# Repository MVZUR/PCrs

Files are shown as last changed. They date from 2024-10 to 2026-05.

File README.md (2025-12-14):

# PCrs
Onboard Computer & System for cheap 4T scooters to improve safety and expand functionalities. <br>
It can be also used with 2T scooters but code modifications is necessary - particularly the RPM counting fragment.

Vehicle used for testing: Benda BD50QT-14

# Functionalities:
- date & time  
- automatic lights (daily / pass)
- hazard warning lights
- RPM indicator
- engine temperature indicator
- stand sensor controll
- tamper alarm
- accelleration measurement
- envirionment condition measurement & alerts

# Revisions:
- <b>v1.0</b> - *do not use* - the first version of the Computer. Many mistakes were made in this version, what makes it unable to use.
- <b>v1.1</b> - *do not use* - works on prototype board, but doesn't work in the target system. Computer got damaged but its unable to diagnose due to hermetic case.
- <b>v2.0</b> - *do not use* - the second version of the Computer. Only power section tested.
- <b>v2.1</b> - *do not use* - second version of the Computer with improved power section. Works in laboratory environment. LCD power controll not working properly.
- <b>v3.0</b> - *under tests* - the third version of the Computer.

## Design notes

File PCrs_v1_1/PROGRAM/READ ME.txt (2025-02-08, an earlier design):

Clock time can be set through physical buttons on dashboard by User in this version of the code (instead of using programmer and change it in code).

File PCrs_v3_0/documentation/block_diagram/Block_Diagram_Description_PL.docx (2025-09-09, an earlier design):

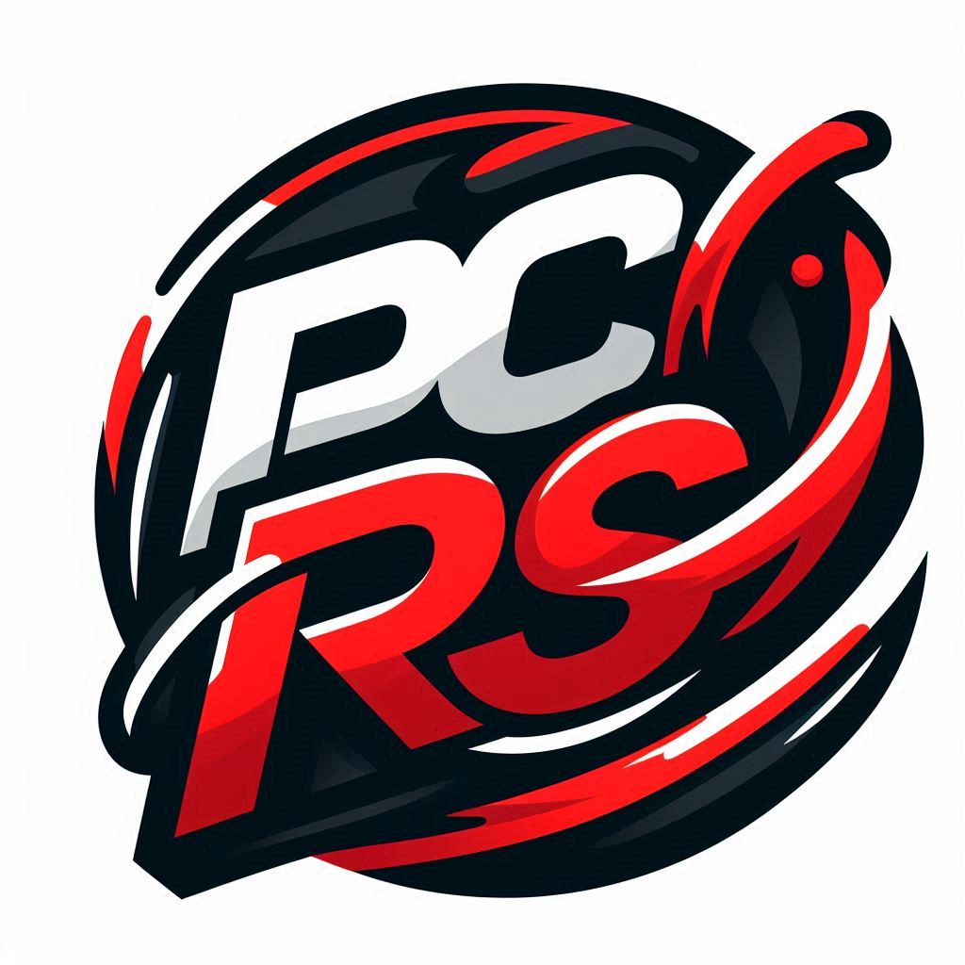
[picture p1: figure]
Obraz zawierający logo, Grafika, symbol, clipart Zawartość wygenerowana przez sztuczną inteligencję może być niepoprawna.

PCrs v3.0

Komputer pokładowy dla jednośladów

Opis połączeń na podstawie schematu blokowego

Opracował: Maksymilian Mazur

1. Alternator:
(źródło zasilania AC)

Źródło napięcia AC generowane przez stator silnika podczas jego obrotu. Jest wykorzystywane do rozruchu silnika, a także podawane na prostownik w celu jego wyprostowania.

Oznaczenie sygnału na schemacie blokowym: AC

2. Rectifier:
(prostownik)

Wyprostowane napięcie z alternatora o wartości +12V. Wartość prądu dostarczanego przez prostownik ściśle zależy od prędkości obrotowej silnika. Prostownik dostarcza zasilanie do świateł pojazdu (diody LED oraz żarówka światła drogowego/mijania).

Oznaczenie sygnału na schemacie blokowym: +12V rect

3. Scooter Battery:
(akumulator, źródło zasilania +12V)

Akumulator zapewnia lokalne napięcie +12V i prąd dostarczany w sposób ciągły. Napięcie to zostaje wykorzystane jako detekcja przekręcenia klucza w stacyjce, zasilanie klaksonu, modułu migacza, a także jest podawana na linię zabezpieczającą dalsze peryferia i wykorzystującą w tym celu układ E-Fuse.

Oznaczenie sygnału na schemacie blokowym: +12V bat

4. E-Fuse:
(zabezpieczona linia zasilania)

Zabezpieczone napięcie zasilania +12V, dostarczane do przetwornicy typu buck, obniżającej napięcie do +5V, a także do cewek wszystkich przekaźników w systemie, pracujących z napięciem +12V.

Zastosowane zabezpieczenia:

- przed zbyt dużym prądem (nadprądowe)
- przed zbyt dużym napięciem (nadnapięciowe)
- zabezpieczenie przed odwrotną polaryzacją (reverse-polarity)
- filtracja napięcia zasilania
- zastosowanie kondensatorów magazynujących energię

Oznaczenie sygnału na schemacie blokowym: +12V protected

5. Buck Converter 12V to 5V:
(przetwornica impulsowa, źródło zasilania +5V)

Przetwornica impulsowa pozwala na obniżenie zabezpieczonego napięcia +12V do napięcia +5V, przy niskim współczynniku strat. Odpowiada za zasilanie wszystkich peryferiów pracujących z napięciem +5V (aktualnie brak). Dostarcza także napięcie do regulatora liniowego LDO, obniżającego napięcie do +3.3V.

Oznaczenie sygnału na schemacie blokowym: +5V

6. LDO Regulator 5V to 3.3V:
(regulator liniowy, źródło zasilania +3.3V)

Regulator liniowy LDO zapewnia zasilanie +3.3V, obniżając napięcie +5V z przetwornicy typu buck. Napięcie +3.3V po uprzedniej filtracji jest dostarczane do głównego mikrokontrolera sterującego całym systemem, a także czujnika warunków środowiskowych, oraz akcelerometru.

Oznaczenie sygnału na schemacie blokowym: +3.3V

7. CR2032 RTC Battery 3V:

(bateria zasilająca moduł zegara czasu rzeczywistego)

Bateria typu CR2032 o napięciu 3V zamocowana w podstawce, zapewniająca zasilanie modułu RTC w stanie uśpienia procesora (brak przekręconego klucza w stacyjce).

Oznaczenie sygnału na schemacie blokowym: RTC pwr

8. Blinker module:
(moduł migacza)

Zasilany z napięcia +12V dostaczanego bezpośrednio z akumulatora. Generuje sygnał o przebiegu prostokątnym, który jest przełączany na kierunkowskazy (lewy lub prawy) za pomocą wbudowanego przełącznika Slide Switch Blinkers.

W zaprojektowanym systemie sygnał ten może być również podawany na klakson i dwa kierunkowskazy jednocześnie w funkcji alarmu, lub świateł awaryjnych. Za łączenie sygnału kierunkowskazów odpowiada przekaźnik typu SPST. Procedura uruchamiająca światła awaryjne jest wyzwalana przyciskiem Hermetic Switch Blinkers, natomiast procedura alarmu jest wyzwalana odczytem z akcelerometru.

Oznaczenie sygnału na schemacie blokowym: pulse 12V

9. Spark module:

(moduł iskrownika)

Moduł odpowiedzialny za dostarczanie impulsu elektrycznego do świecy zapłonowej. Nie wytwarza impulsów, jeśli czujnik otwarcia stopki bocznej dostarcza do niego potencjał GND. Impulsy z modułu iskrownika są przekazywane do głównego mikrokontrolera, który na ich podstawie oblicza prędkość obrotową silnika.

10. Starter:

(rozrusznik)

Jest odpowiedzialny za rozruch silnika. Aby rozrusznik zakręcił silnikiem, musi otrzymać fazę AC – podawaną z alternatora poprzez dźwignię hamulca Brake Lever (switch) , oraz masę GND – podawaną z przycisku zapłonu Ignition Button. Przycisk zapłonu podaje GND na rozrusznik tylko wtedy, gdy czujnik otwarcia stopki bocznej dostarcza do niego GND, lub gdy czujnik ten jest wyłączony (masa podawana jest wtedy przez przekaźnik.

11. Stand sensor:

(czujnik otwarcia stopki bocznej)

Czujnik wbudowany w pojazd. Jest zamocowany na podnóżku i działa jak przełącznik typu slide, który przesuwa się wraz z ruchem podnóżka. Przy złożonym podnóżku podaje masę GND na przycisk zapłonu Ignition Button. Przy rozłożonym podnóżku podaje masę na moduł zapłonowy przerywając tym samym wysyłanie impulsów do wytworzenia iskry. Skutkuje to zgaszeniem silnika w przypadku otworzenia podnóżka podczas jego pracy (nie występuje zapalenie mieszanki).

12. Przełączniki wbudowane:

Horn Switch – przycisk monostabilny wciskany NO, sterowanie klaksonem.
Zastosowana dioda zabezpieczająca na wypadek wciśnięcia podczas działania alarmu (stan niski impulsu).

Slide Switch Blinkers – przełącznik bistabilny przesuwany NO trójpozycyjny, sterowanie kierunkowskazami. Brak zabezpieczenia w przypadku wciśnięcia w trakcie działania świateł awaryjnych (impuls jest taki sam).

Brake Lever (Switch) – przycisk monostabilny wciskany NO (przycisk w formie dźwigni hamulca), podanie fazy AC na rozrusznik w momencie wciśnięcia.
Wymusza trzymanie hamulca w chwili uruchamiania silnika.

Ignition Button – przycisk monostabilny wciskany NO, podanie masy na rozrusznik w celu uruchomienia silnika. Masa jest dostarczana do przycisku przez czujnik otwarcia stopki bocznej lub przekaźnik (gdy czujnik jest wyłączony).

Light Switch LED / PASS (Manual) – przełącznik bistabilny NC dwupozycyjny, wybór pomiędzy światłami do jazdy dziennej (LED) lub światłami mijania/drogowymi. Przełącznik podaje zasilanie na wybrany rodzaj świateł jeśli tryb ich pracy jest ustawiony jako manual – wówczas do przełącznika dostarczane jest zasilanie z przekaźnika SPDT.

Pass Light Switch LOW / HIGH (Manual) – przełącznik bistabilny NC dwupozycyjny, wybór pomiędzy światłami mijania lub drogowymi. Podaje zasilanie na włókno do oświetlenia w trybie mijania lub włókno do oświetlenia w trybie drogowym żarówki. Do przełącznika dostarczane jest zasilanie z przełącznika Light Switch LED / PASS (Manual) w trybie PASS, lub z przekaźnika SPDT wysterowanego przez fotorezystor.

13. Przełączniki dodatkowe, na potrzeby działania systemu:

Hermetic Switch Blinkers – przycisk monostabilny wciskany NO, włączanie/wyłączanie świateł awaryjnych. Wysyła sygnał cyfrowy do MPU (zapamiętanie stanu poprzedniego).

Hermetic Switch Display Menu – przycisk monostabilny wciskany NO, zmiana treści na ekranie OLED. Wysyła sygnał cyfrowy do MPU (zapamiętanie stanu poprzedniego).

Hermetic Switch Display Set – przycisk monostabilny wciskany NO, zmiana/zatwierdzanie parametrów na ekranie. Wysyła sygnał cyfrowy do MPU (zapamiętanie stanu poprzedniego).

Toggle Switch Stand Sensor ON/OFF – przełącznik bistabilny hebelkowy NO, włączanie/wyłączanie czujnika otwarcia stopki bocznej. Wysyła sygnał cyfrowy do MPU (sprawdzanie stanu przełącznika, informowanie o zmianach na ekranie i po restarcie systemu).

14. Czujniki:

Accelerometer Sensor – akcelerometr wykrywający ruch i przyspieszenie pojazdu. Odpowiada za uruchamianie procedur awaryjnych (światła awaryjne przy gwałtownym hamowaniu), oraz alarmu.

Ambience, Temperature, Humidity, Pressue Sensor – czujnik warunków środowiskowych. Pomiary i informacja na ekranie. Na podstawie jego odczytów wysyłane są ostrzeżenia o zagrożeniach wynikających z pogody.

Photoresistor Sensor – czujnik zmierzchowy, oparty na fotorezystorze. Na podstawie jego odczytów dokonywany jest wybór świateł w trybie automatycznym.

Engine Temperature Sensor – termistorowy czujnik temperatury silnika. Informacja o aktualnej temperaturze silnika jest wyświetlana na ekranie.

15. Pozostałe peryferia:

SWD Programming Interface – interfejs programowania głównego mikrokontrolera sterującego systemem.

Oled Display – ekran oled interfejsu graficznego dla użytkownika.

(xxxx) Relay – (typ) przekaźnik klasy automotive.

Relay Driver – sterownik cewki przekaźnika, oparty na tranzystorze MOS.

High Side Switch – przełącznik dużej mocy, do sterowania sygnałami.

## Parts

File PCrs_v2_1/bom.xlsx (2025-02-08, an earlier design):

Bill of materials PCrs 2.0
Name | Model | Quantity | Description
Atmega32A AU | TQFP44 (SMD) | 1 | MPU (main AVR unit) current draw up to 15mA
crystal oscillator 8MHz | 8.00M-CFPX104 | 1 | AVR power section
relay | RM513011851005 | 4 | high current control coil current draw up to 72mA*4 = 288mA
schottky diode | 1N5819HW-7-F | 4 | relay flyback diode
transistor N-channel | 2N7002-7-F | 4 | to drive relays by MPU, vehicle key detection (idle control)
DC-DC buck converter | TPS54202DDCR | 1 | 12V to 5V
ISP KANDA connector | ZL231-10PG | 1 | ISP programming interface connector
24pin connector | MX-5569-24A2 | 1 | I/O connector
4pin connector | MX-39-30-1040 | 1 | power connector
goldpin x3 | ZL201-40G | 1 | reset jumper
resistor 511k (499k) | ERJ3EKF4993V | 1 | buck converter enable resistor (optional)
resistor 105k | WR06X1053FTL | 1 | buck converter enable resistor (optional)
resistor 49.9R | WR06X49R9FTL | 1 | buck converter output resistor
resistor 100k | WR06X1003FTL | 1 | buck converter output resistor
resistor 13.3k | WR06X1332FTL | 1 | buck converter output resistor
resistor 220k | RC0603FR-07220K | 1 | vehicle key voltage divider
resistor 150k | WR06X1503FTL | 1 | vehicle key voltage divider
resistor 50k | AR0603-50K-0.1% | 1 | FOTO sensor pullup
resistor 10k | WR06X103JTL | 3 | reset pullup, RPM counter pulldown, TMP sensor pullup
capacitor 1uF | 0603B105K160CT | 1 | buck converter input cap
capacitor 75pF | C0603C750J5GAC | 1 | buck converter feedback cap
capacitor 10uF | CL10A106KP8NNNC | 1 | buck converter input cap
capacitor 100nF | 0603B104K500CT | 6 | buck converter boot cap, AVR power section, decap
capacitor 22uF | GRM188R61A226ME15D | 2 | buck converter output cap
capacitor 22pF | 06035C220JAT2A | 2 | AVR power section (crystal oscillator)
inductor 10uH | LQM18DN100M70L | 1 | AVR power section
inductor 15uH | HPI0630-150 | 1 | power section

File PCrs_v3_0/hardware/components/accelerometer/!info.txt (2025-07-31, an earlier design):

************************* MODELS: *************************
***********************************************************

-----------
| MPU6050 |
-----------

- interface: I2C

- datasheet:
https://invensense.tdk.com/wp-content/uploads/2015/02/MPU-6000-Datasheet1.pdf

- STM example code:
https://github.com/lamik/MPU6050_STM32_HAL

- shop:
https://sklep.msalamon.pl/produkt/mpu6050-modul/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

__________________________________________________________________________________________________________________

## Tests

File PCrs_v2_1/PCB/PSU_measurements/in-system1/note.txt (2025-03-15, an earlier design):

Switching voltage regulator in-system measurements were made with 20MHz bandwidth limit, 100Ohm resistive load & following capacitors: 100uF input electrolytic cap & 88uF output ceramic caps

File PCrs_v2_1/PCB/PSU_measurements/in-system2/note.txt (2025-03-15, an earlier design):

Switching voltage regulator in-system measurements were made with 20MHz bandwidth limit, 100Ohm resistive load & following capacitors: 220uF input electrolytic cap, 220uF output electrolytic cap & 88uF output ceramic caps

Note that electrolytic capacitors are THD (Trough Hole Devices) & have higher inductance on their terminals which affects the voltage ripple (current resonance effect)

See the pictures in this folder for test configuration.

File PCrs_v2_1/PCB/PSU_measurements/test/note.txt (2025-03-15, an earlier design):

Switching voltage regulator test measurements were made with 20MHz bandwidth limit, 100Ohm resistive load & electrolytics capacitors

For example:
OUT 33uCap - stands for additional 33uF electrolytic capacitor on output of the buck converter
IN 100uCap - stands for additional 100uF electrolytic capacitor on input of the buck converter

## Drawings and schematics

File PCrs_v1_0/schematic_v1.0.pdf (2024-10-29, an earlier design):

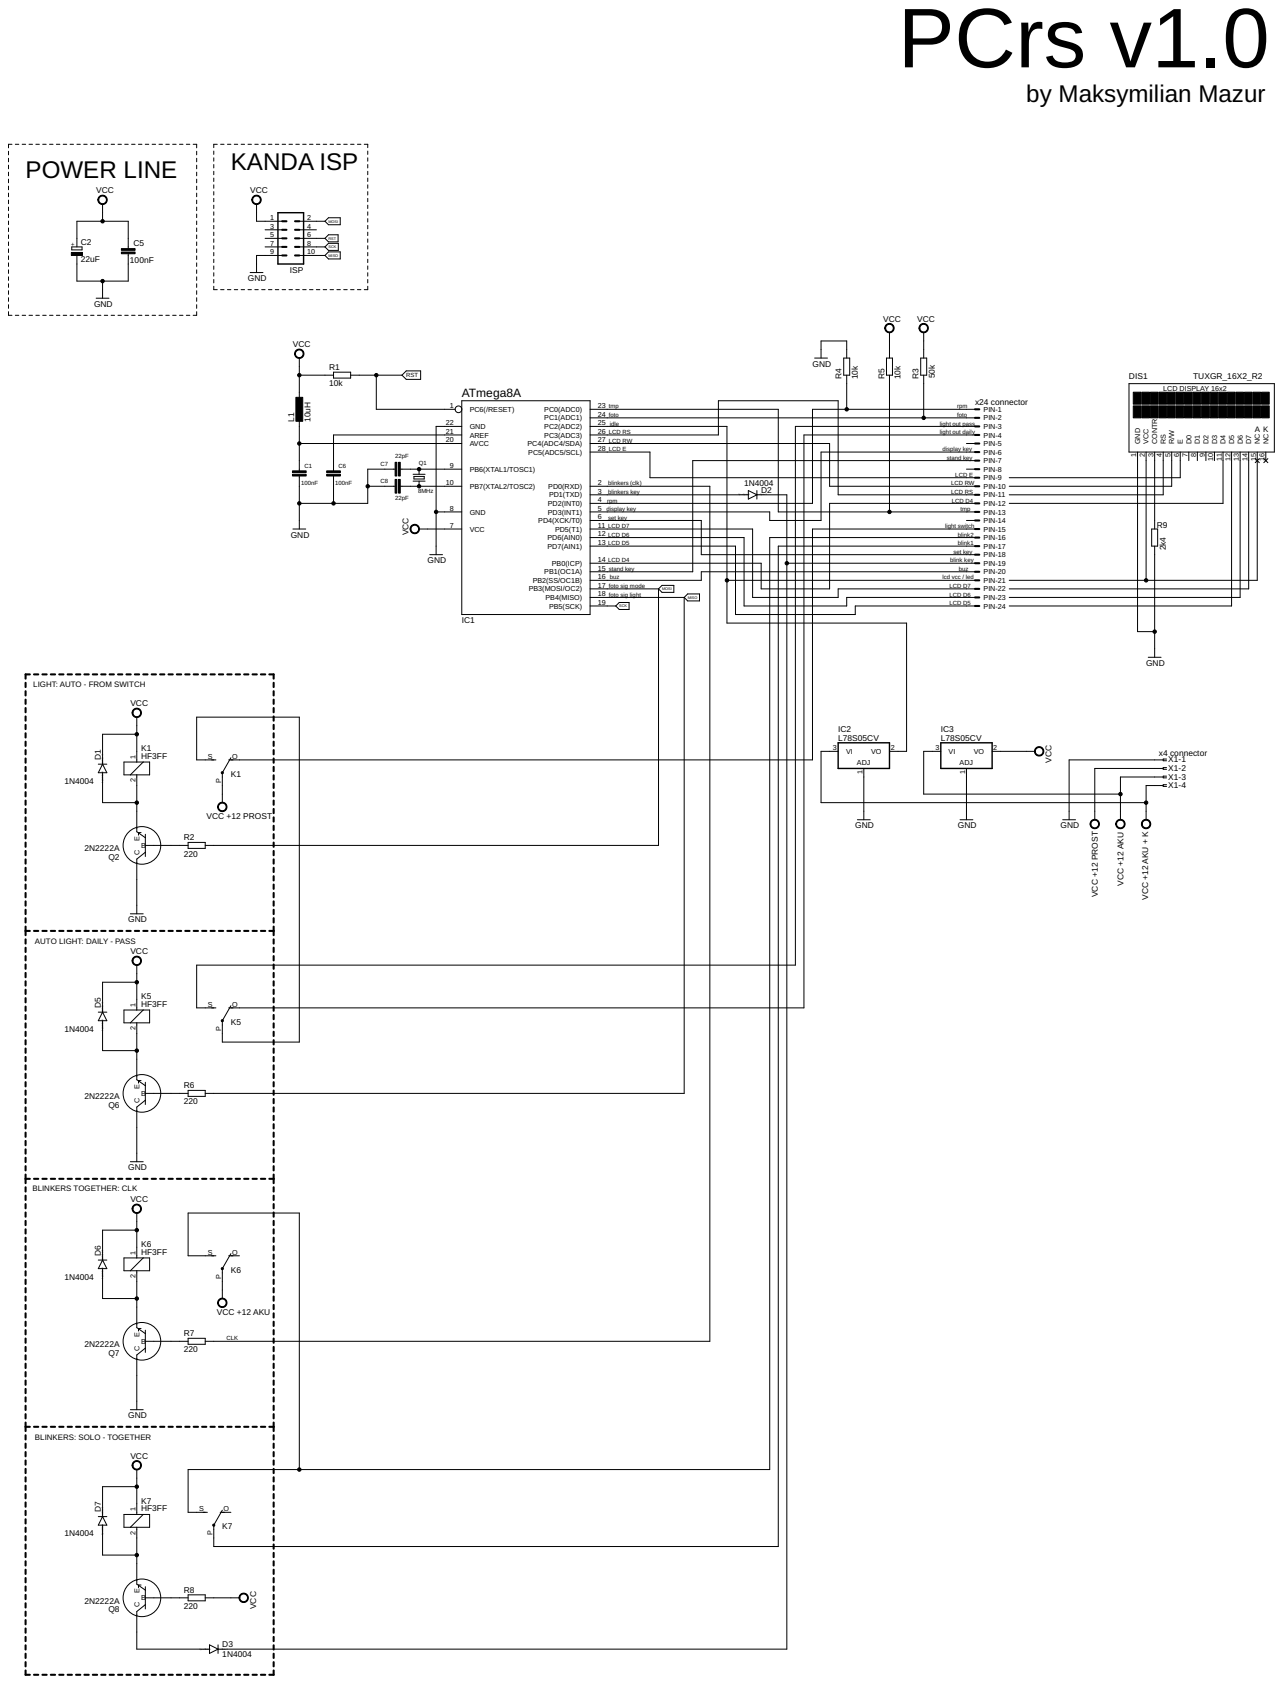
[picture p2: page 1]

SpiceOrder 1 SpiceOrder 2 SpiceOrder 1 SpiceOrder 2 SpiceOrder 1 SpiceOrder 2 KANDA ISP POWER LINE

PIN-1 PIN-2 PIN-3 PIN-4 PIN-5 PIN-6 PIN-7 PIN-8 PIN-9 PIN-10 PIN-11 PIN-12 PIN-13 PIN-14 PIN-15 PIN-16 PIN-17 PIN-18 PIN-19 PIN-20 PIN-21 PIN-22 PIN-23 PIN-24

idle
LCD RS

stand key display key

blinkers key

rpm
display key

LCD D7
LCD D6
LCD D5

LCD D4
stand key

LIGHT: AUTO - FROM SWITCH

VCC +12 PROST VCC +12 AKU

AUTO LIGHT: DAILY - PASS

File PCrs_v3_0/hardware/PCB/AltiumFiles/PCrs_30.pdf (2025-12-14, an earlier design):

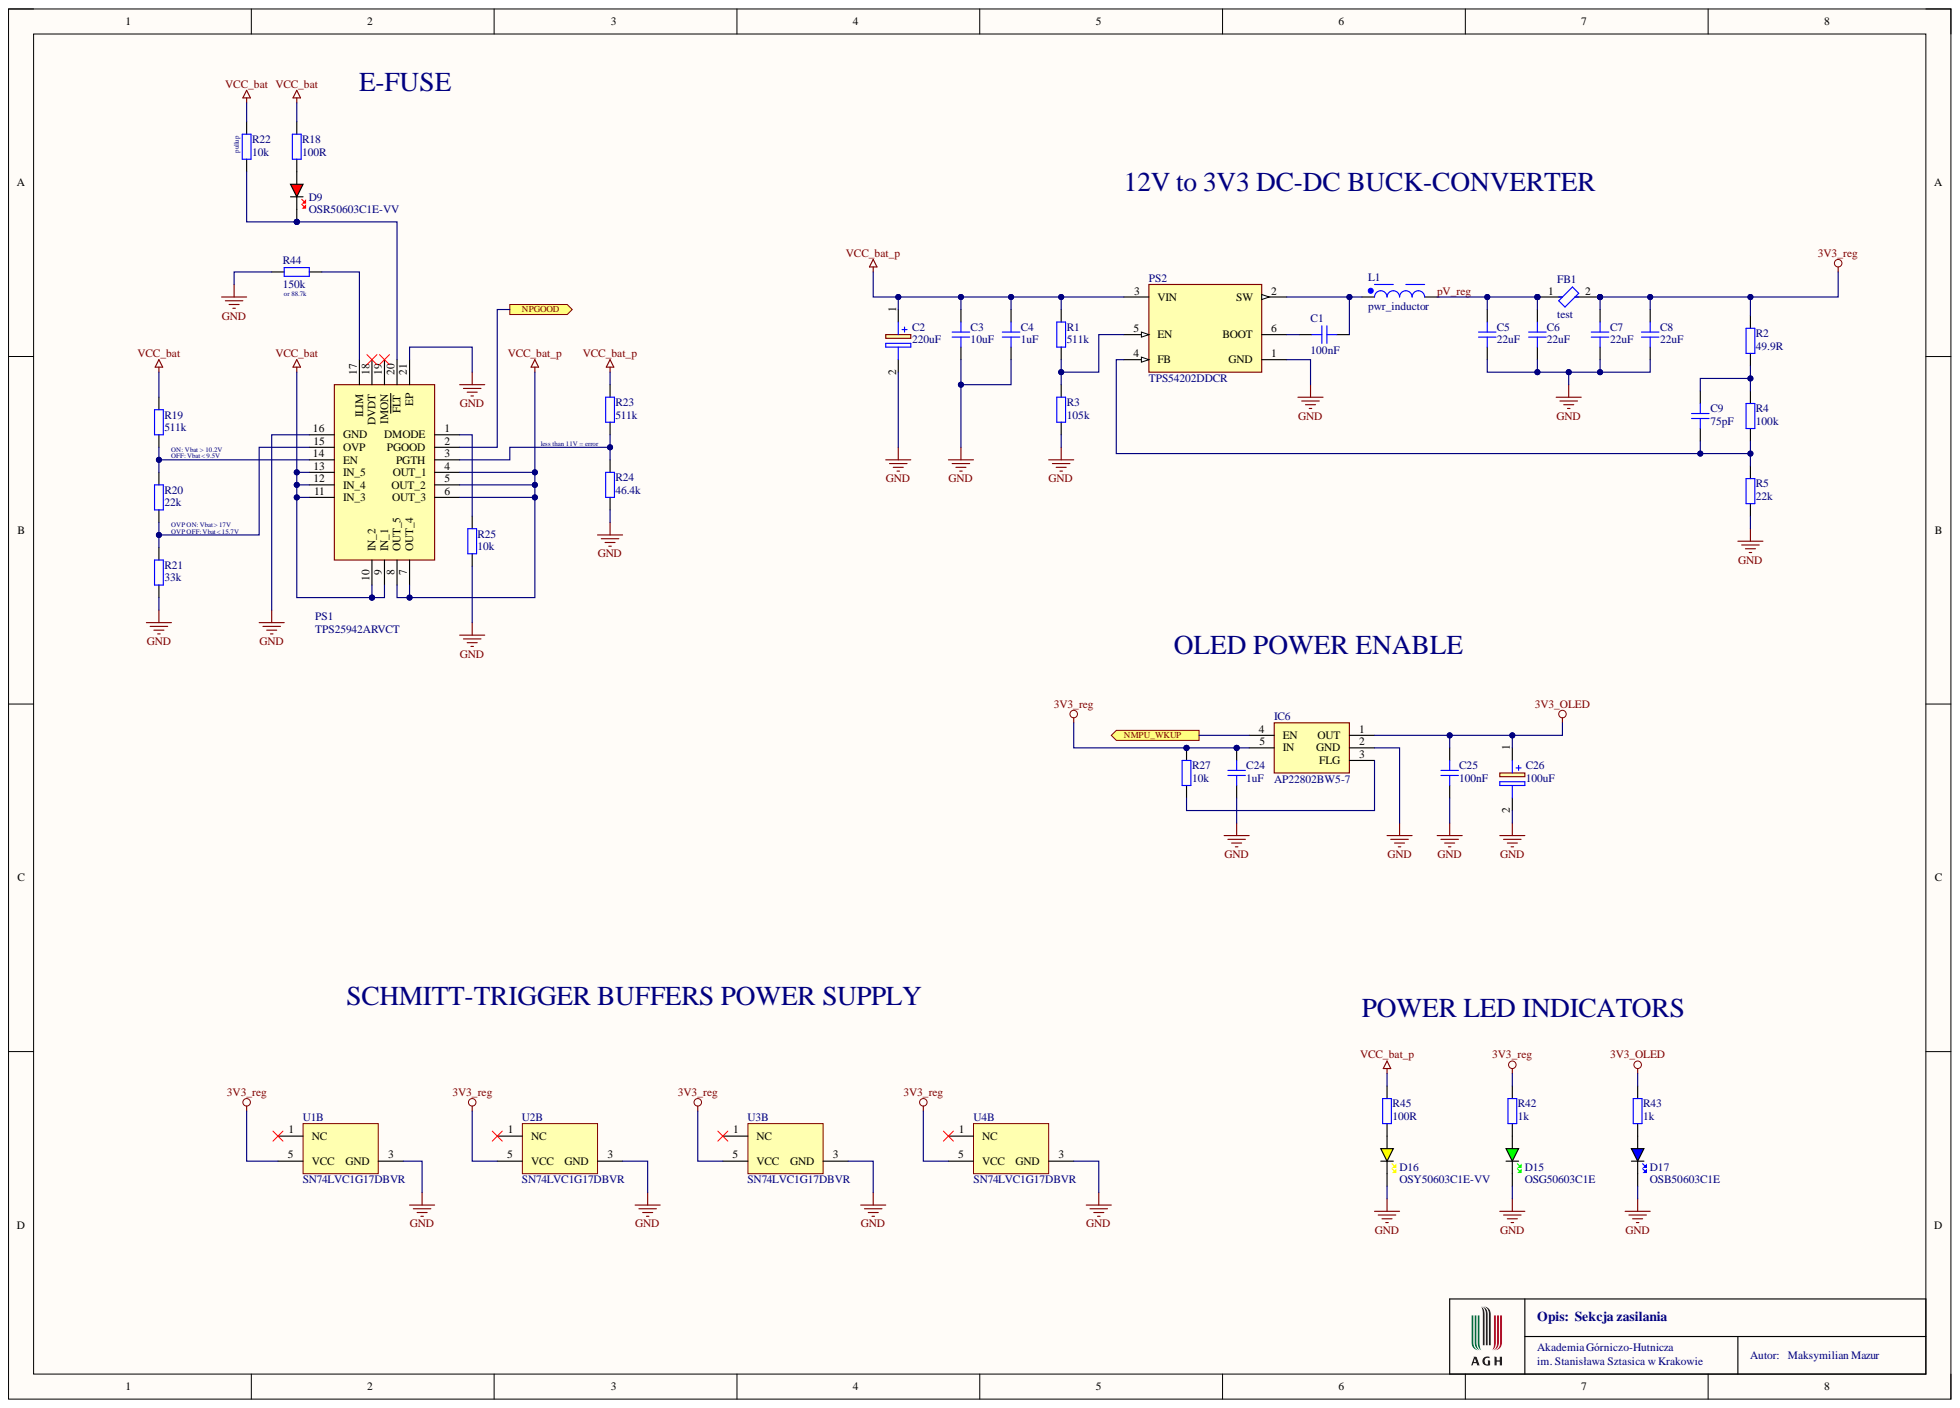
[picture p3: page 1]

12V to 3V3 DC-DC BUCK-CONVERTER

EP 21 FLT 20 IMON 19 DVDT 18 ILIM 17

less than 11V = error ON: Vbat > 10.2V OFF:Vbat< 9.5V

OVP ON:Vbat> 17V OVP OFF:Vbat< 15.7V

SCHMITT-TRIGGER BUFFERS POWER SUPPLY

Opis: Sekcja zasilania

im. Stanisława Sztasica w Krakowie | Autor: Maksymilian Mazur Akademia Górniczo-Hutnicza

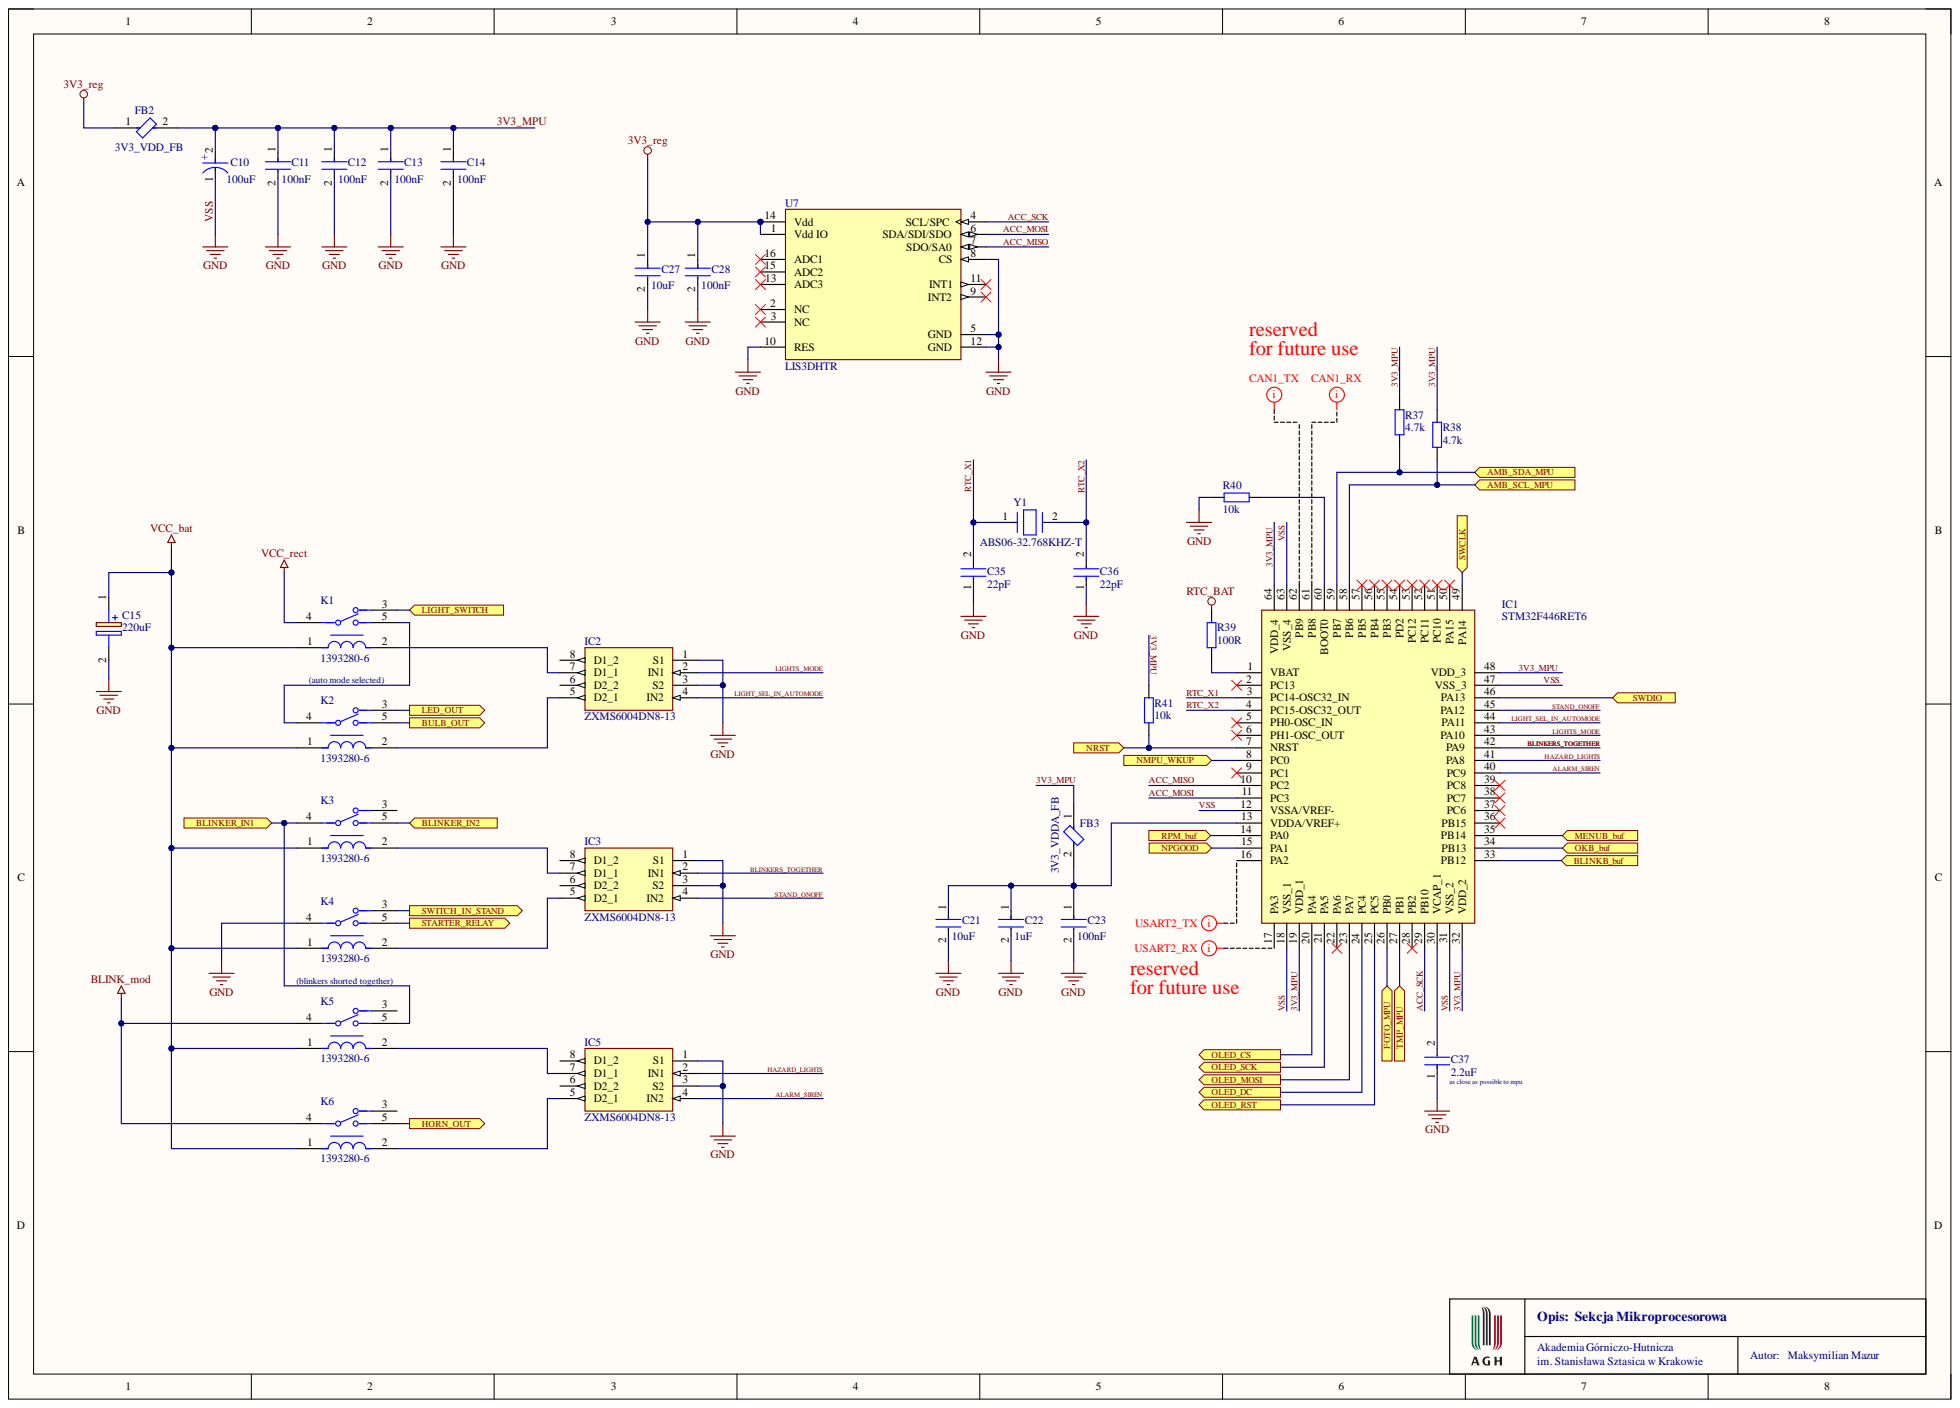
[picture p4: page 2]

as close as possible to mpu

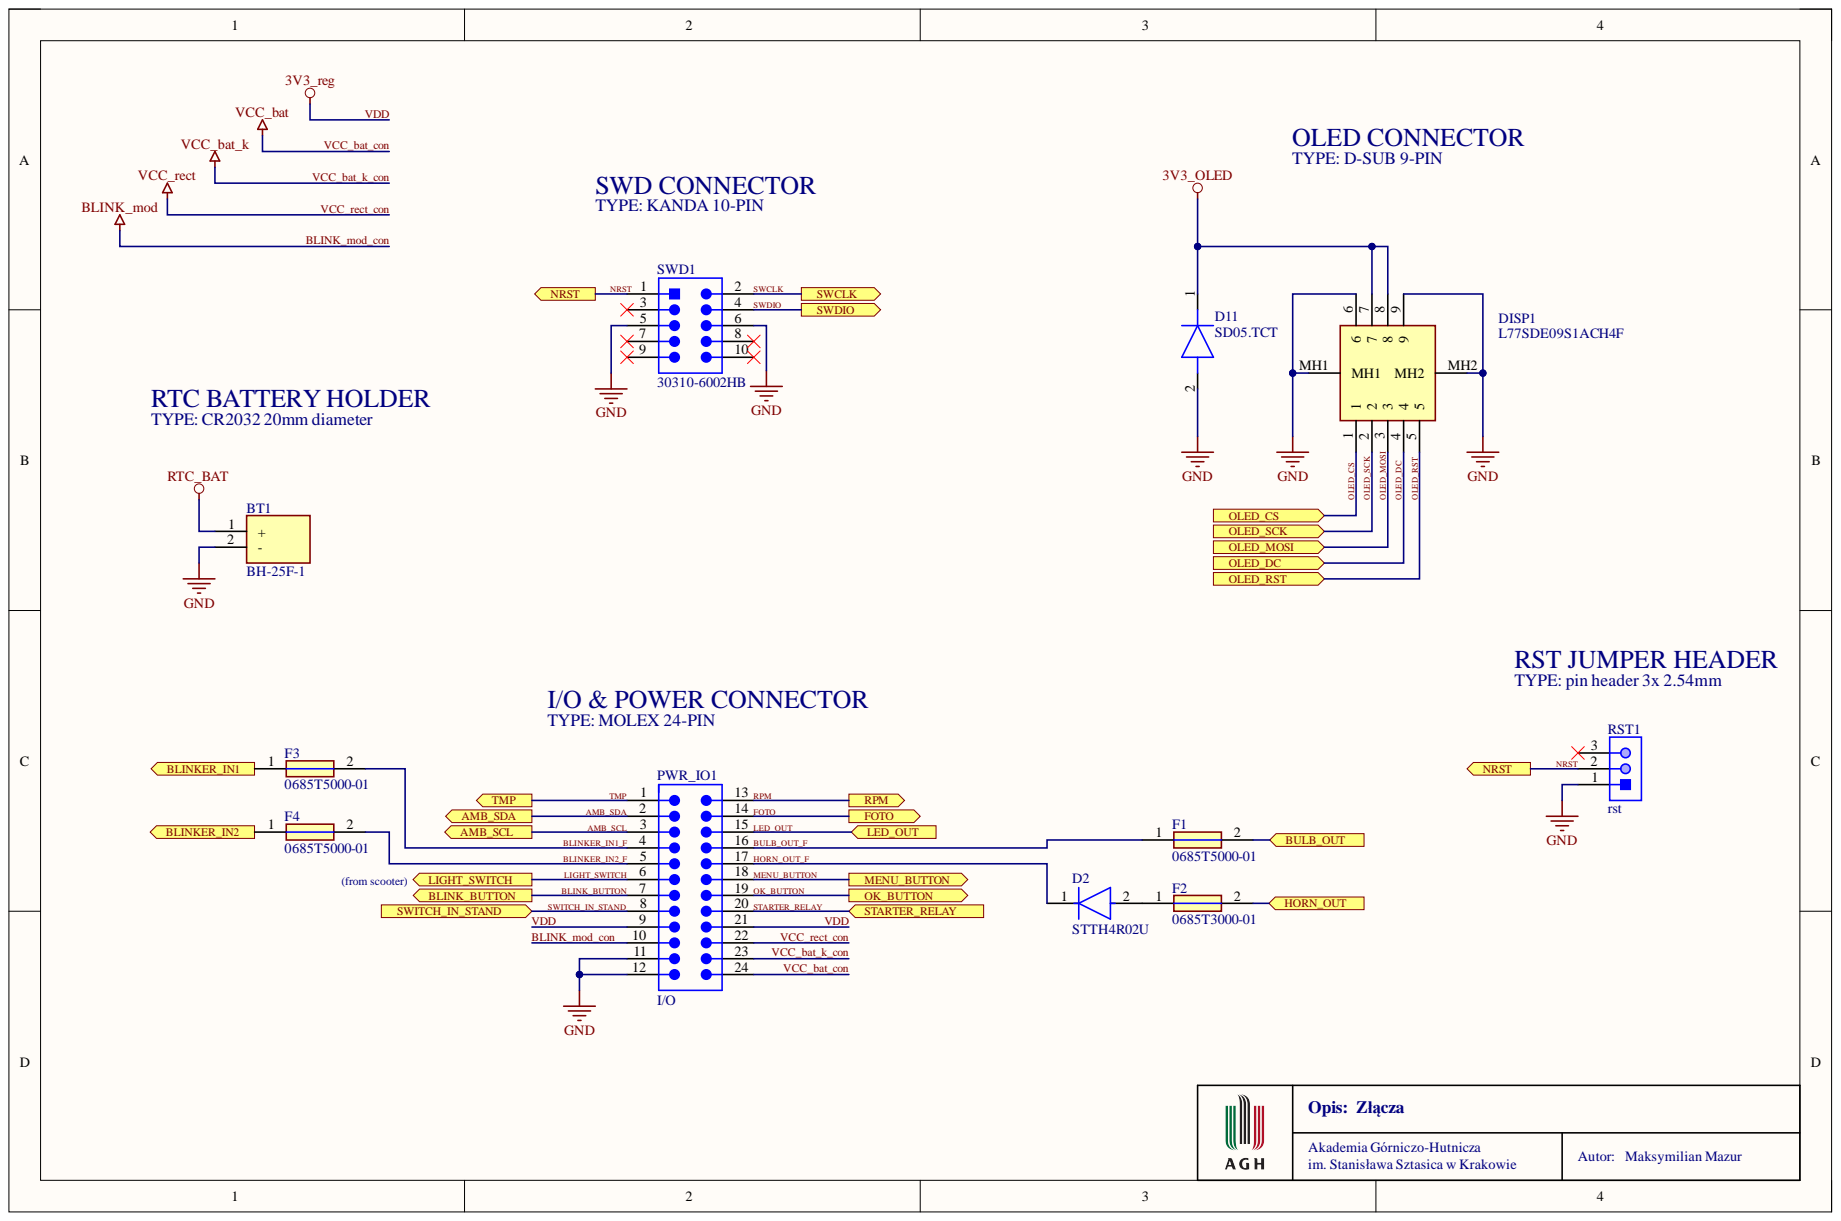
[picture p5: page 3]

Opis: Złącza

Autor: Maksymilian Mazur Akademia Górniczo-Hutnicza

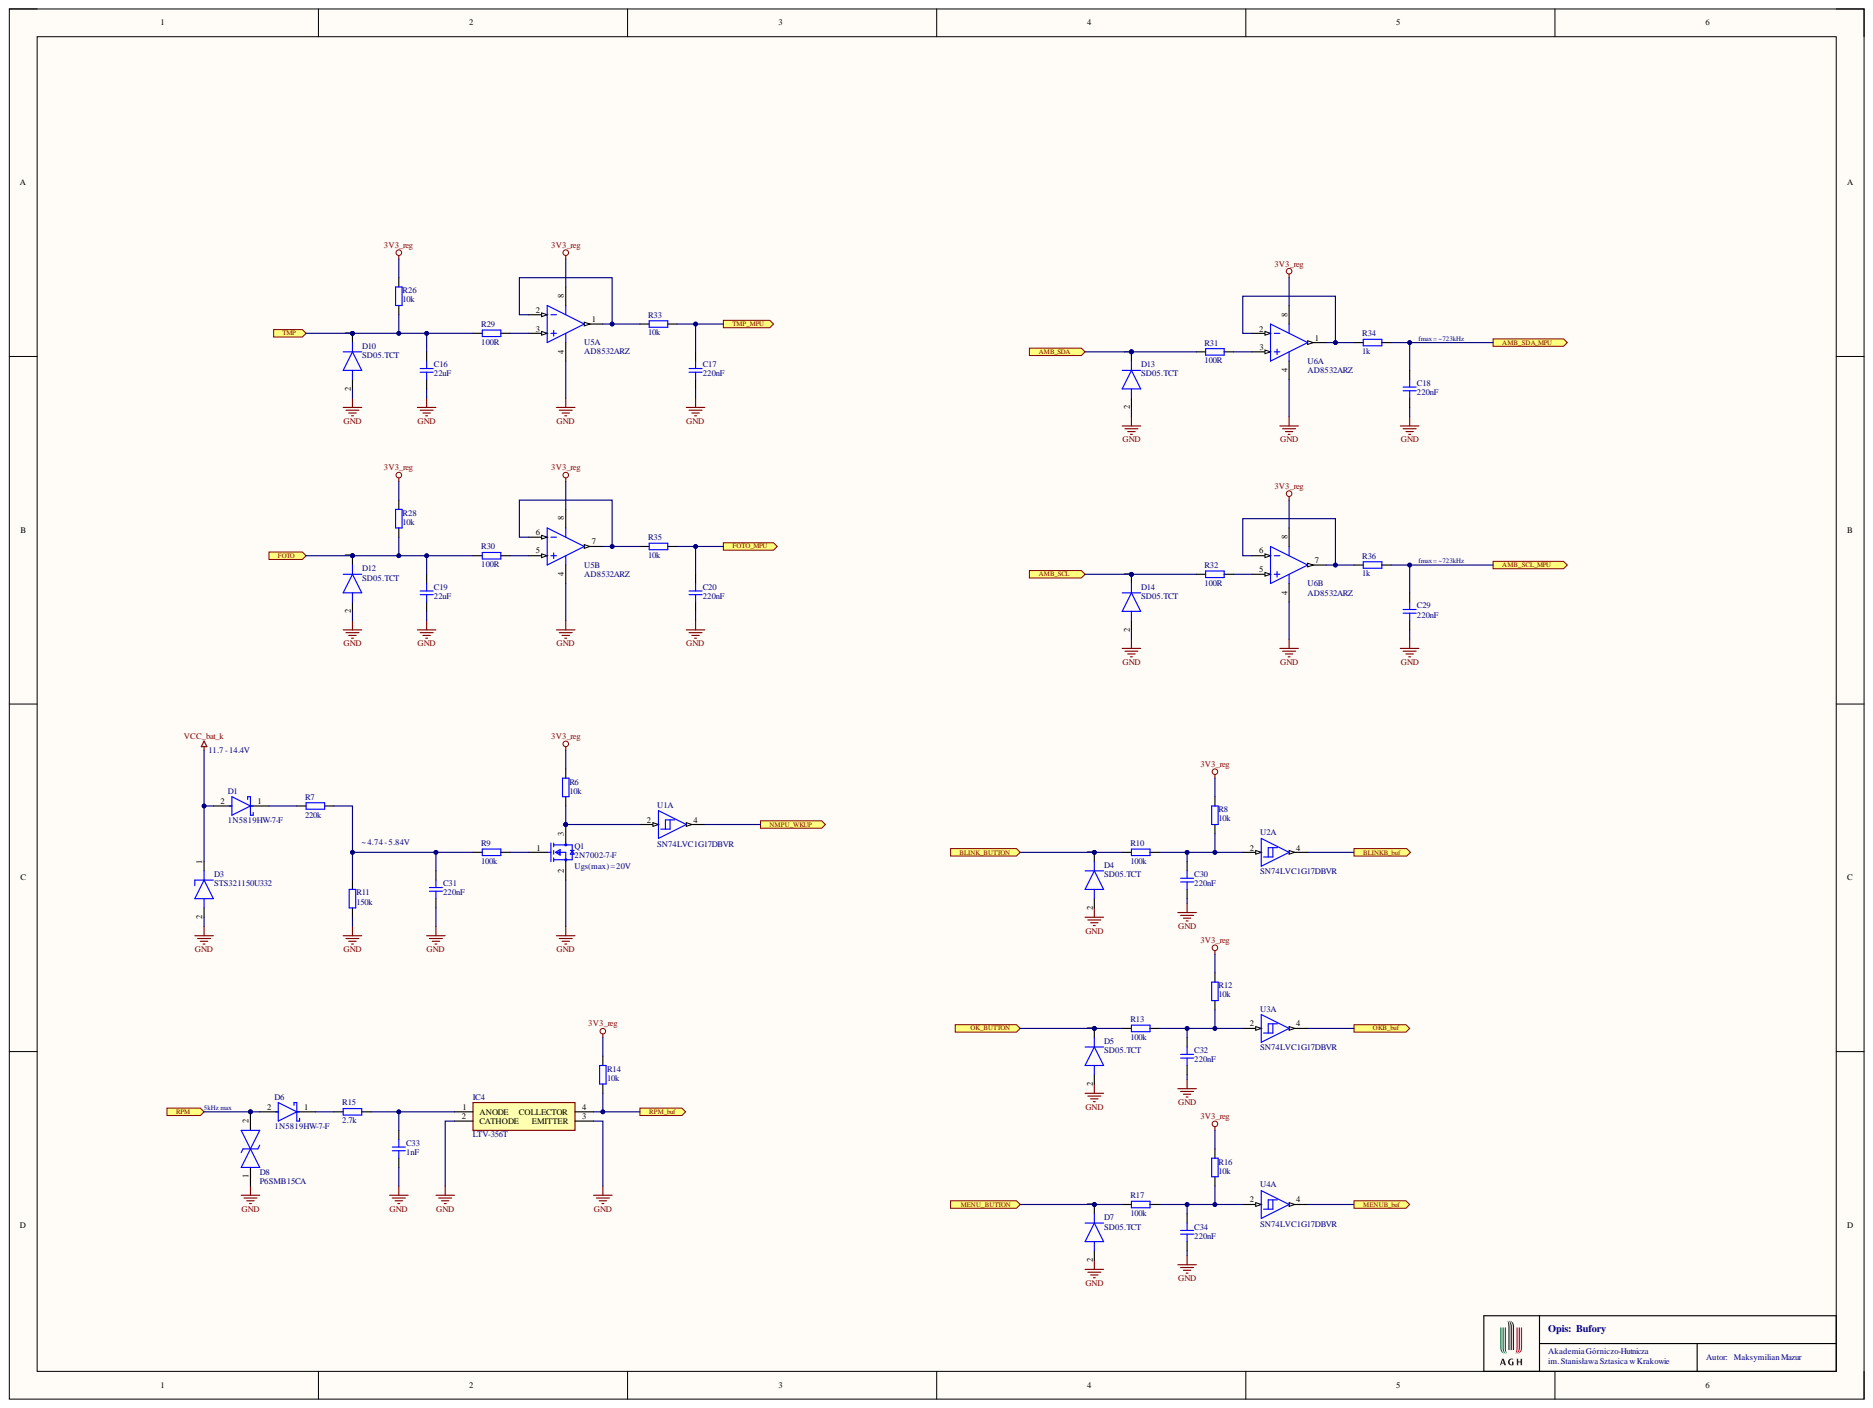
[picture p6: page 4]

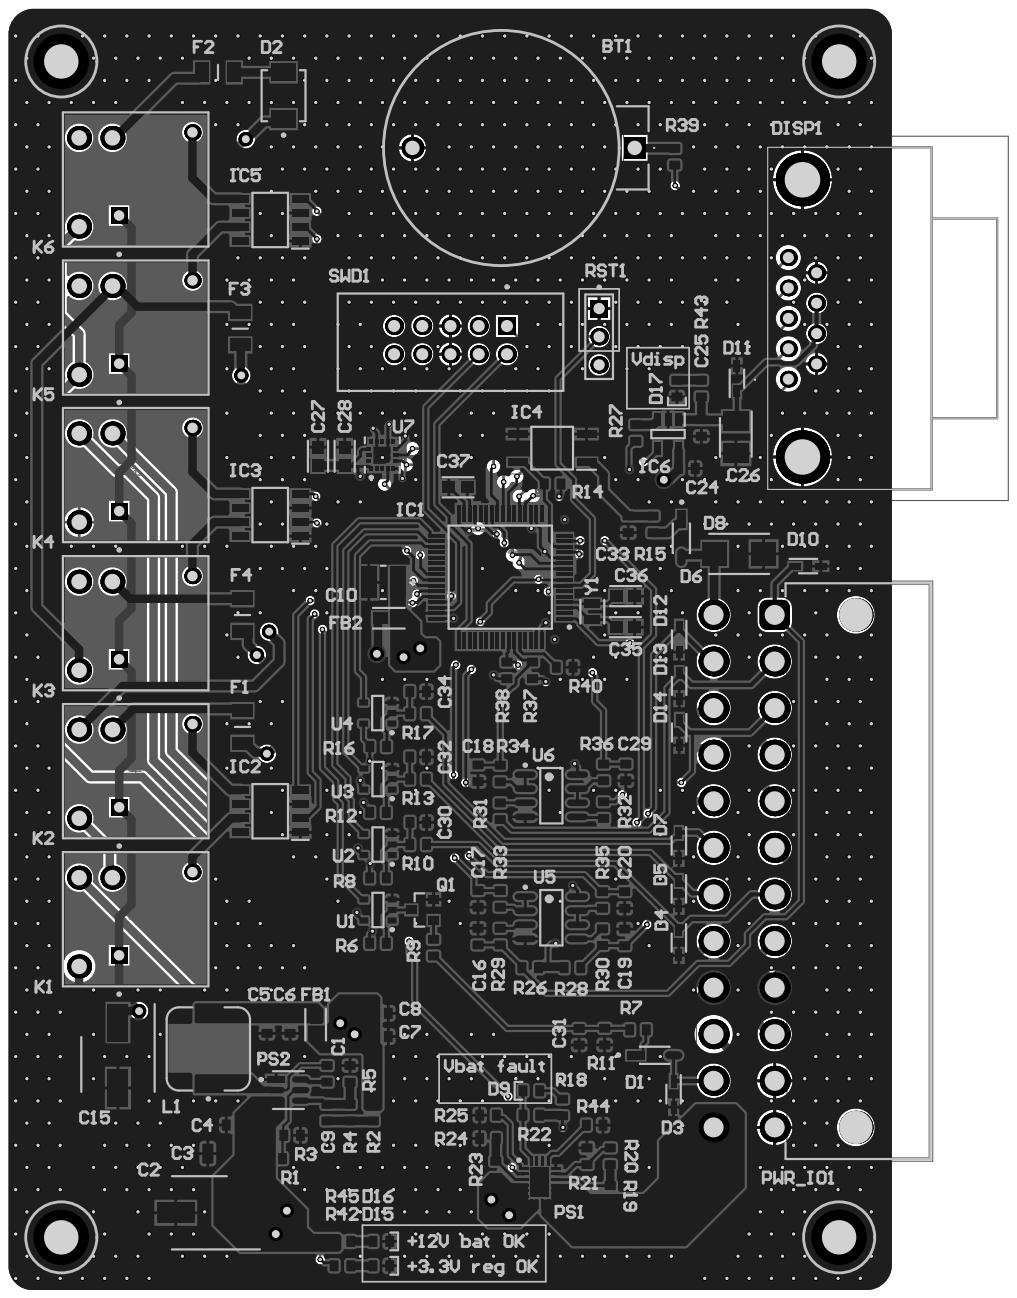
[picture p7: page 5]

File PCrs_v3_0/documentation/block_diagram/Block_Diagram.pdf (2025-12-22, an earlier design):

# LEGEND:

# - build into the vehicle system

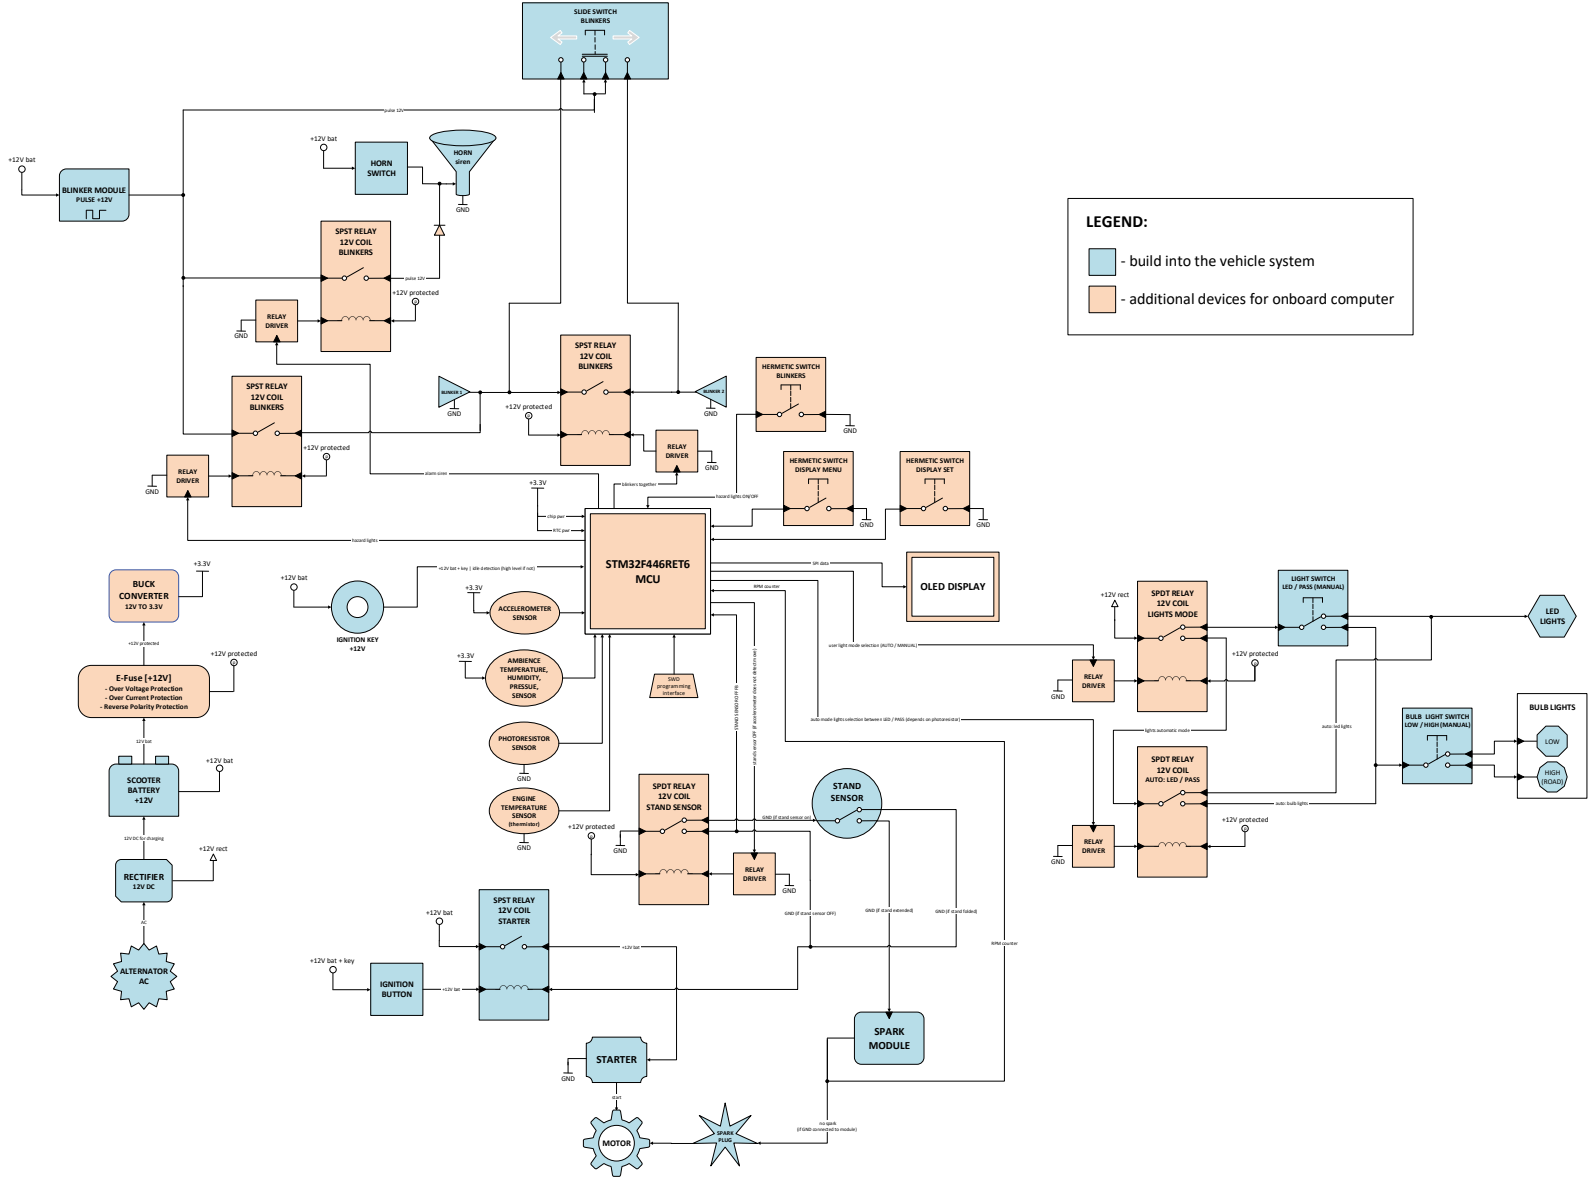
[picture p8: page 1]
STM32F446RET6 MCU; SCOOTER BATTERY +12V; ALTERNATOR AC; RECTIFIER; IGNITION KEY +12V; PHOTORESISTOR SENSOR; ACCELEROMETER SENSOR; AMBIENCE TEMPERATURE, HUMIDITY, PRESSUE, SENSOR; ENGINE TEMPERATURE SENSOR (thermistor); GND; 12V bat; RTC pwr; BLINKER MODULE PULSE +12V; HORN SWITCH; pulse 12V; BLINKER 1; BLINKER 2; HERMETIC SWITCH BLINKERS; HERMETIC SWITCH DISPLAY MENU; SPST RELAY 12V COIL BLINKERS; RELAY DRIVER; blinkers together; IGNITION BUTTON; STARTER; start; +12V bat; STAND SENSOR; RELAY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

- additional devices for onboard computer

hazard lights ON/OFF

+12V bat + key | idle detection (high level if not)

LIGHT SWITCH
LED / PASS (MANUAL)

user light mode selection (AUTO / MANUAL)

DRIVER stand sensor OFF ⁽if accelerometer does not detect move⁾

E-Fuse [+12V]
- Over Voltage Protection
- Over Current Protection
- Reverse Polarity Protection

STAND SENSOR OFF FB

BULB LIGHT SWITCH
LOW / HIGH (MANUAL)

auto mode lights selection between LED / PASS (depends on photoresistor)

auto: led lights

lights automatic mode

SPDT RELAY
12V COIL
AUTO: LED / PASS

auto: bulb lights

GND (if stand sensor on)

12V DC for charging

GND (if stand extended)

GND (if stand folded)

GND (if stand sensor OFF)

(if GND connected to module)

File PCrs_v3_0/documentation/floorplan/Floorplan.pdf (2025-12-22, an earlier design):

# LEGEND:

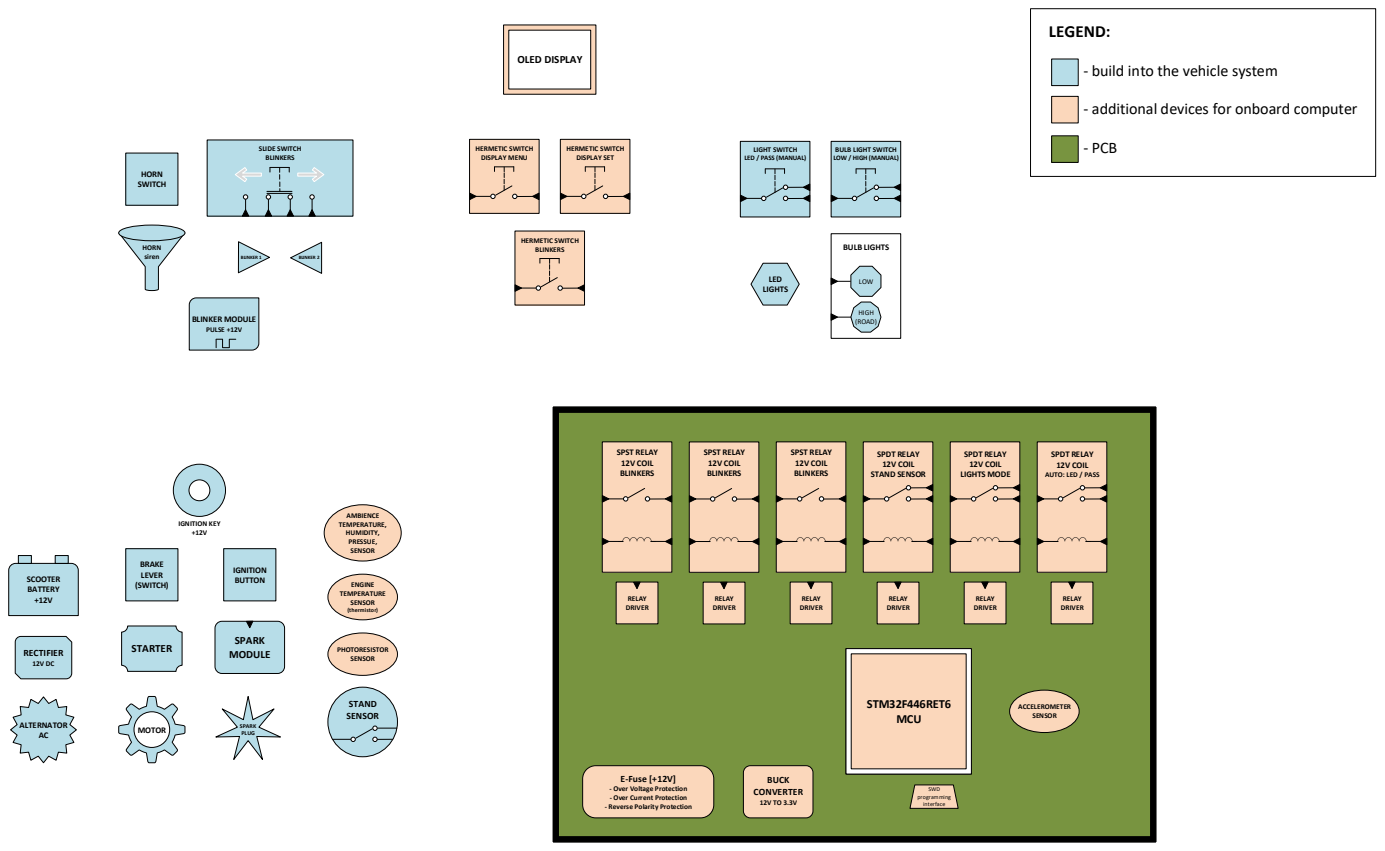
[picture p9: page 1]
STM32F446RET6 MCU; SCOOTER BATTERY +12V; ALTERNATOR AC; RECTIFIER; IGNITION KEY +12V; PHOTORESISTOR SENSOR; ACCELEROMETER SENSOR; AMBIENCE TEMPERATURE, HUMIDITY, PRESSUE, SENSOR; ENGINE TEMPERATURE SENSOR (thermistor); BLINKER MODULE PULSE +12V; HORN SWITCH; BLINKER 1; BLINKER 2; HERMETIC SWITCH BLINKERS; HERMETIC SWITCH DISPLAY MENU; SPST RELAY 12V COIL BLINKERS; RELAY DRIVER; BRAKE LEVER (SWITCH); STARTER; IGNITION BUTTON; STAND SENSOR; SPDT RELAY 12V COIL STAND SENSOR; MOTOR; SPARK; PLUG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

- build into the vehicle system

- additional devices for onboard computer

LIGHT SWITCH
LED / PASS (MANUAL)

BULB LIGHT SWITCH
LOW / HIGH (MANUAL)

SPDT RELAY
12V COIL
AUTO: LED / PASS

E-Fuse [+12V]
- Over Voltage Protection
- Over Current Protection
- Reverse Polarity Protection

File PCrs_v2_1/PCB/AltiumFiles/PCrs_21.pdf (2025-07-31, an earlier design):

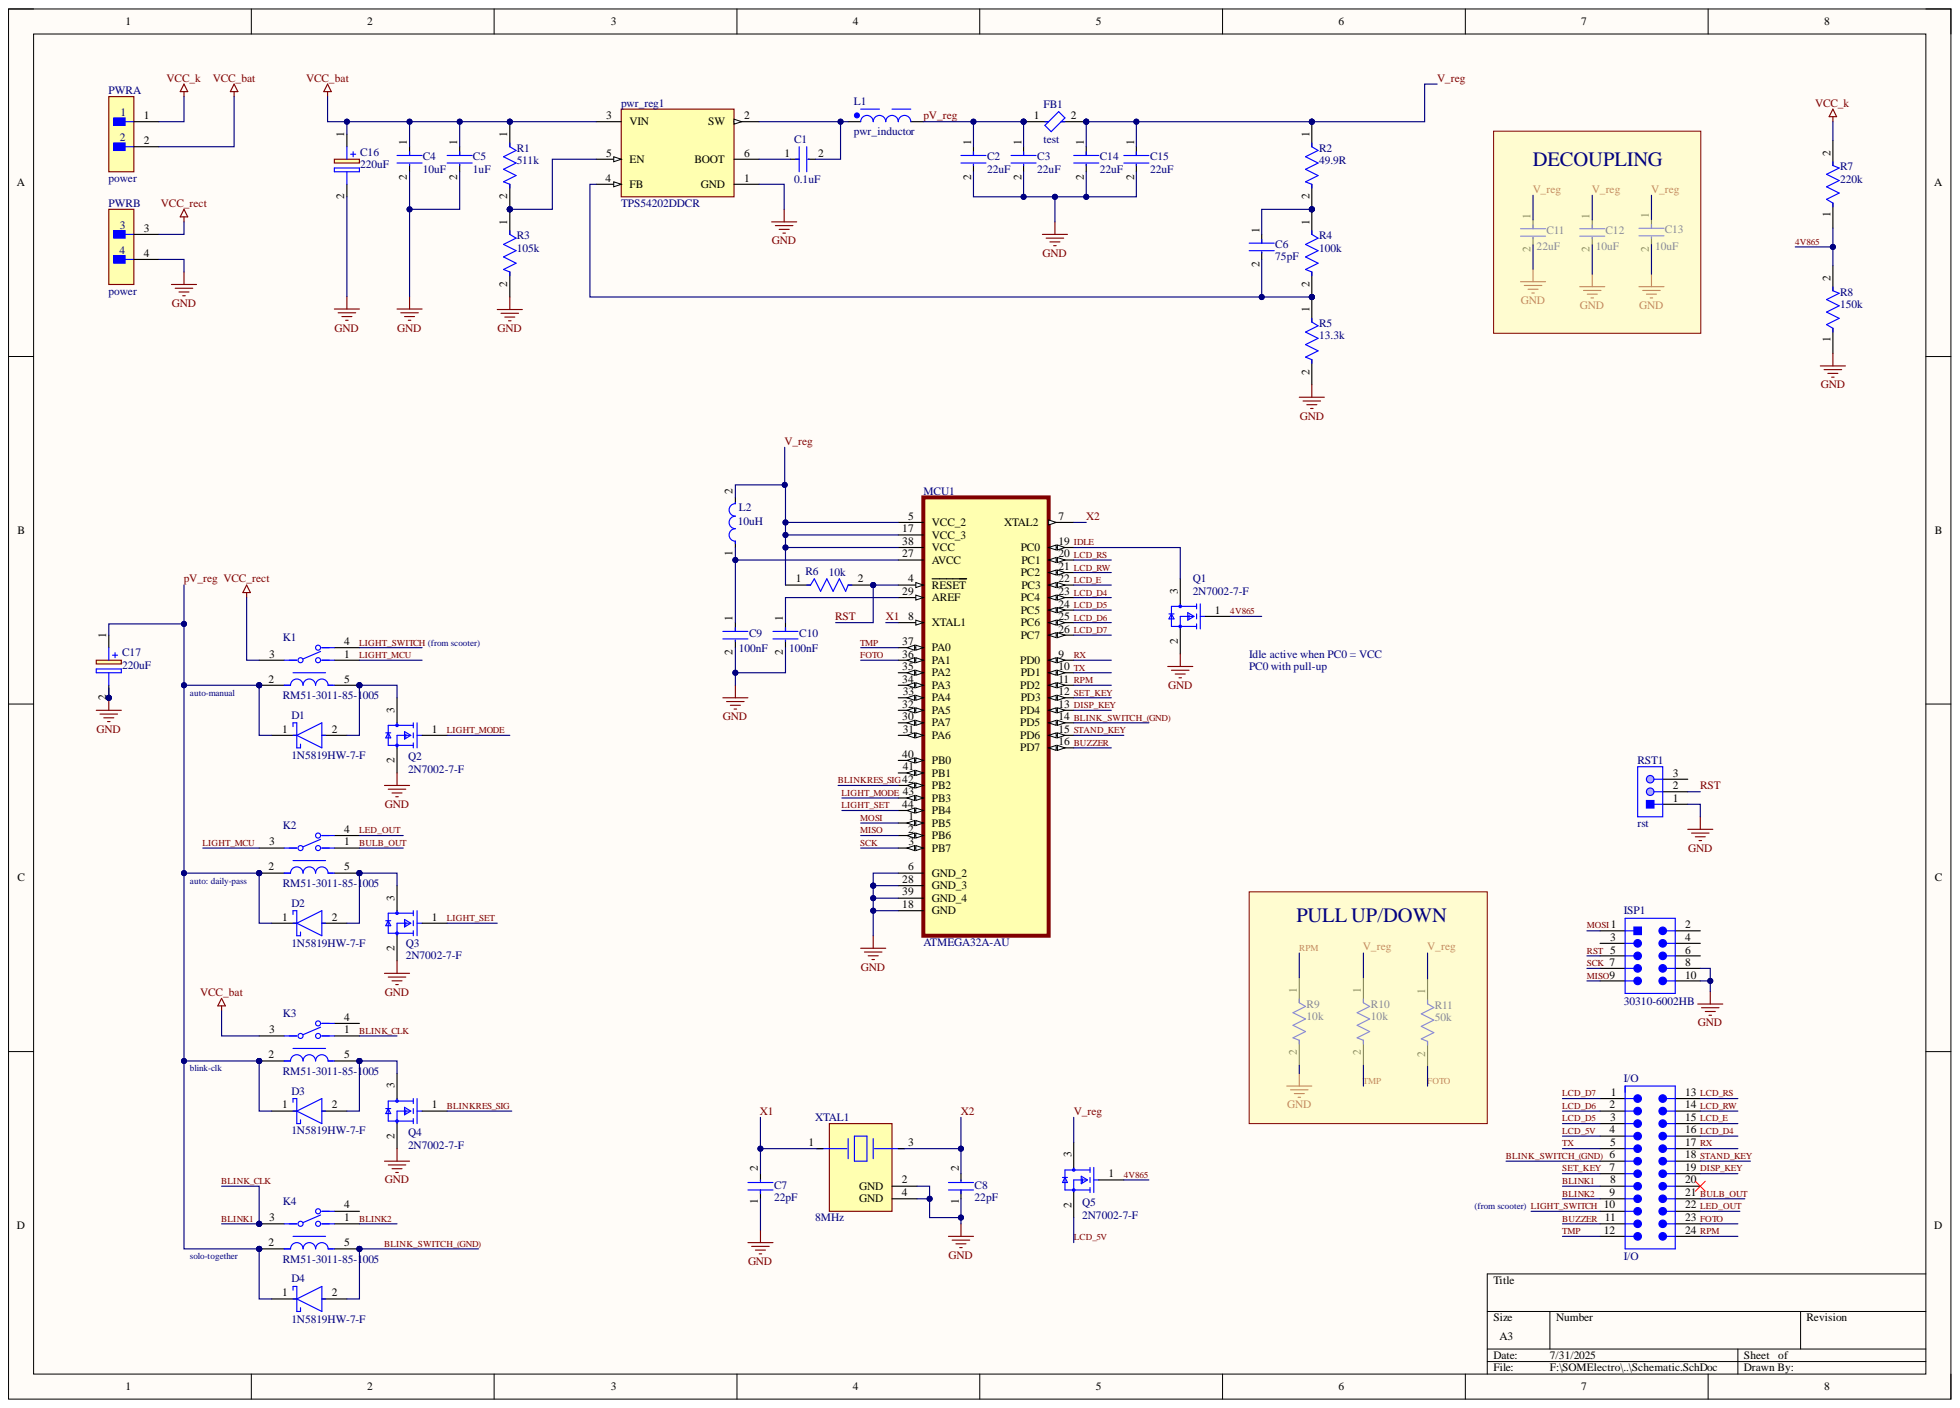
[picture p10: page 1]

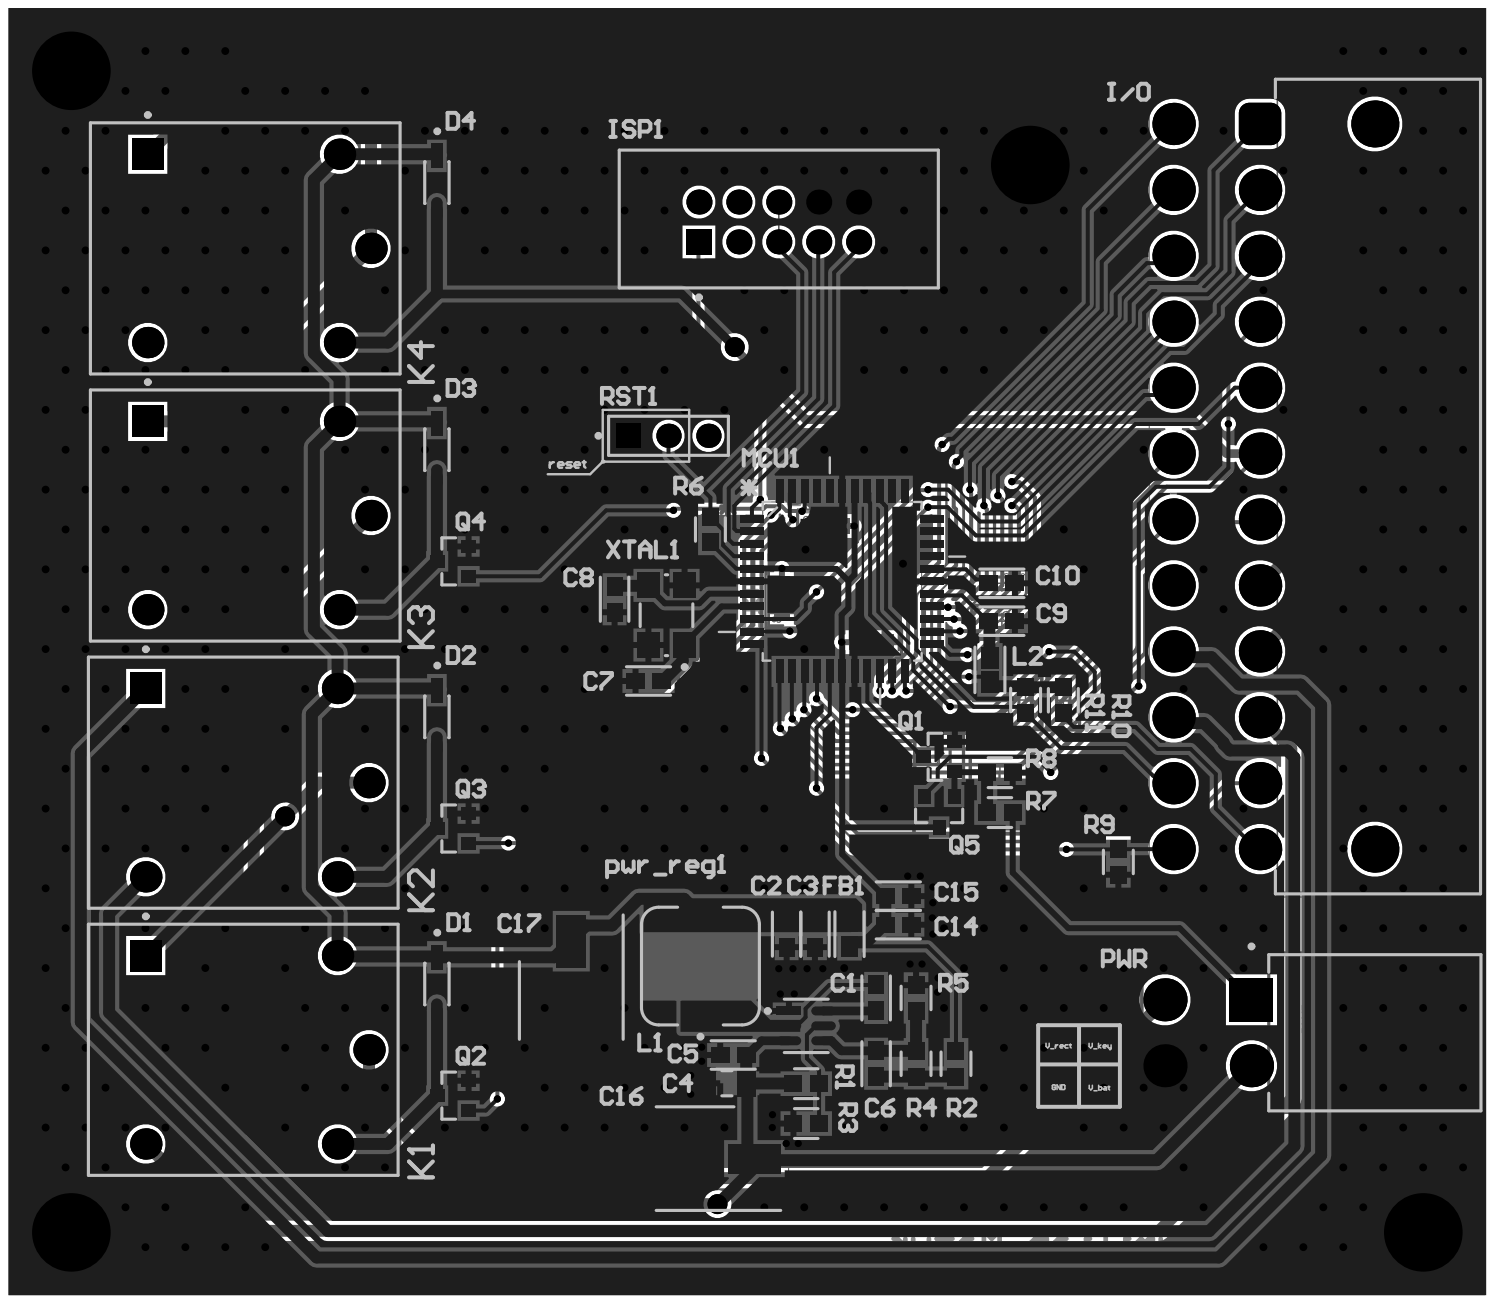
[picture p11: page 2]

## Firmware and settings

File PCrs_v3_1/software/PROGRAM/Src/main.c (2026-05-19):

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
/* Includes ------------------------------------------------------------------*/
#include "main.h"

/* USER CODE BEGIN Includes */
#include "ssd1306.h"
/* USER CODE END Includes */

ADC_HandleTypeDef hadc1;

FMPI2C_HandleTypeDef hfmpi2c1;

I2C_HandleTypeDef hi2c1;

RTC_HandleTypeDef hrtc;

SPI_HandleTypeDef hspi1;
SPI_HandleTypeDef hspi2;
SPI_HandleTypeDef hspi3;

TIM_HandleTypeDef htim1;
TIM_HandleTypeDef htim2;

void SystemClock_Config(void);
static void MX_GPIO_Init(void);
static void MX_ADC1_Init(void);
static void MX_FMPI2C1_Init(void);
static void MX_RTC_Init(void);
static void MX_SPI1_Init(void);
static void MX_SPI2_Init(void);
static void MX_SPI3_Init(void);
static void MX_TIM2_Init(void);
static void MX_I2C1_Init(void);
static void MX_TIM1_Init(void);
/* USER CODE BEGIN PFP */
void tasker(void);
void displayer(void);
/* USER CODE END PFP */

/**
  * @brief  The application entry point.
  * @retval int
  */
int main(void)
{

  /* MCU Configuration--------------------------------------------------------*/

  /* Reset of all peripherals, Initializes the Flash interface and the Systick. */
  HAL_Init();

  /* Configure the system clock */
  SystemClock_Config();

  /* Initialize all configured peripherals */
  MX_GPIO_Init();
  MX_ADC1_Init();
  MX_FMPI2C1_Init();
  MX_RTC_Init();
  MX_SPI1_Init();
  MX_SPI2_Init();
  MX_SPI3_Init();
  MX_TIM2_Init();
  MX_I2C1_Init();
  MX_TIM1_Init();
  /* USER CODE BEGIN 2 */
  ssd1306_Init();
  clock_init();

  //HAL_TIM_Base_Start_IT(&htim1);	//start timer1 interrupts - always on for hazard lights

  //HAL_GPIO_WritePin(GPIO_Output_relaydrvr_lights_mode_GPIO_Port, GPIO_Output_relaydrvr_lights_mode_Pin,1);
  //relay_test(FULL);
  photo_sensor_test();
	//HAL_GPIO_WritePin(GPIO_Output_relaydrvr_alarm_siren_GPIO_Port, GPIO_Output_relaydrvr_alarm_siren_Pin,1);

	//HAL_GPIO_WritePin(GPIOx, GPIO_Pin, PinState)
  /* USER CODE END 2 */

  /* Infinite loop */
  /* USER CODE BEGIN WHILE */
  while (1)
  {

//	  displayer();
//	  tasker();
	  //HAL_Delay(10);	// TODO to simulate

    /* USER CODE END WHILE */

    /* USER CODE BEGIN 3 */
  }
  /* USER CODE END 3 */
}

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


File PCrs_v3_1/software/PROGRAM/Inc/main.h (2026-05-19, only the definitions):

#define GPIO_EXTI0_idle_Pin GPIO_PIN_0
#define GPIO_EXTI0_idle_GPIO_Port GPIOC
#define GPIO_EXTI0_idle_EXTI_IRQn EXTI0_IRQn
#define SPI3_MOSI_sensors_Pin GPIO_PIN_1
#define SPI3_MOSI_sensors_GPIO_Port GPIOC
#define SPI2_MISO_accelerometer_Pin GPIO_PIN_2
#define SPI2_MISO_accelerometer_GPIO_Port GPIOC
#define SPI2_MOSI_accelerometer_Pin GPIO_PIN_3
#define SPI2_MOSI_accelerometer_GPIO_Port GPIOC
#define TIM2_CH1_rpm_Pin GPIO_PIN_0
#define TIM2_CH1_rpm_GPIO_Port GPIOA
#define CS_oled_Pin GPIO_PIN_4
#define CS_oled_GPIO_Port GPIOA
#define SPI1_SCK_oled_Pin GPIO_PIN_5
#define SPI1_SCK_oled_GPIO_Port GPIOA
#define SPI1_MOSI_oled_Pin GPIO_PIN_7
#define SPI1_MOSI_oled_GPIO_Port GPIOA
#define DC_oled_Pin GPIO_PIN_4
#define DC_oled_GPIO_Port GPIOC
#define RESET_oled_Pin GPIO_PIN_5
#define RESET_oled_GPIO_Port GPIOC
#define ADC1_IN8_photoresistor_Pin GPIO_PIN_0
#define ADC1_IN8_photoresistor_GPIO_Port GPIOB
#define ADC1_IN9_thermistor_Pin GPIO_PIN_1
#define ADC1_IN9_thermistor_GPIO_Port GPIOB
#define SPI2_SCK_accelerometer_Pin GPIO_PIN_10
#define SPI2_SCK_accelerometer_GPIO_Port GPIOB
#define GPIO_Input_BUTTONblinkers_Pin GPIO_PIN_12
#define GPIO_Input_BUTTONblinkers_GPIO_Port GPIOB
#define GPIO_Input_BUTTONok_Pin GPIO_PIN_13
#define GPIO_Input_BUTTONok_GPIO_Port GPIOB
#define GPIO_Input_BUTTONmenu_Pin GPIO_PIN_14
#define GPIO_Input_BUTTONmenu_GPIO_Port GPIOB
#define FMPI2C1_SCL_sensors_Pin GPIO_PIN_6
#define FMPI2C1_SCL_sensors_GPIO_Port GPIOC
#define FMPI2C1_SDA_sensors_Pin GPIO_PIN_7
#define FMPI2C1_SDA_sensors_GPIO_Port GPIOC
#define GPIO_Output_relaydrvr_alarm_siren_Pin GPIO_PIN_9
#define GPIO_Output_relaydrvr_alarm_siren_GPIO_Port GPIOC
#define GPIO_Output_relaydrvr_hazard_lights_Pin GPIO_PIN_8
#define GPIO_Output_relaydrvr_hazard_lights_GPIO_Port GPIOA
#define GPIO_Output_relaydrvr_blinkers_together_Pin GPIO_PIN_9
#define GPIO_Output_relaydrvr_blinkers_together_GPIO_Port GPIOA
#define GPIO_Output_relaydrvr_lights_mode_Pin GPIO_PIN_10
#define GPIO_Output_relaydrvr_lights_mode_GPIO_Port GPIOA
#define GPIO_Output_relaydrvr_light_sel_Pin GPIO_PIN_11
#define GPIO_Output_relaydrvr_light_sel_GPIO_Port GPIOA
#define GPIO_Output_relaydrvr_stand_onoff_Pin GPIO_PIN_12
#define GPIO_Output_relaydrvr_stand_onoff_GPIO_Port GPIOA
#define SPI3_SCK_sensors_Pin GPIO_PIN_10
#define SPI3_SCK_sensors_GPIO_Port GPIOC
#define SPI3_MISO_sensors_Pin GPIO_PIN_4
#define SPI3_MISO_sensors_GPIO_Port GPIOB

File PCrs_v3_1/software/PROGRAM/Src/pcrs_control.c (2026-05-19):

/*
 * pcrs_control.c
 *
 *  Created on: Sep 5, 2025
 *      Author: mmazur
 */


#include "main.h"

// system status variable
volatile sys_statuses system_status = STATUS_SLEEPING;		// initial value is STATUS_SLEEP to begin power on procedure after turning the key in the ignition

// timer variable
extern TIM_HandleTypeDef htim2;


// ******************************************************************************************
// *               		DISABLING / ENABLING PERIPHERALS CLOCKS / INTERRUPTS		        *
// ******************************************************************************************

// turn on/off GPIO module
void control_GPIO_enable() {
	  __HAL_RCC_GPIOC_CLK_ENABLE();
	  __HAL_RCC_GPIOA_CLK_ENABLE();
	  __HAL_RCC_GPIOB_CLK_ENABLE();
}
void control_GPIO_disable() {

	__HAL_RCC_GPIOC_CLK_DISABLE();
	__HAL_RCC_GPIOA_CLK_DISABLE();
	__HAL_RCC_GPIOB_CLK_DISABLE();
}


// turn on/off ADC1 module
void control_ADC1_enable() {
	__HAL_RCC_ADC1_CLK_ENABLE();
}
void control_ADC1_disable() {
	__HAL_RCC_ADC1_CLK_DISABLE();
}


// turn on/off I2C1 FM+ module
void control_FMPI2C1_enable() {
	  HAL_FMPI2CEx_EnableFastModePlus(FMPI2C_FASTMODEPLUS_SCL);
	  HAL_FMPI2CEx_EnableFastModePlus(FMPI2C_FASTMODEPLUS_SDA);
}
void control_FMPI2C1_disable() {
	  HAL_FMPI2CEx_DisableFastModePlus(FMPI2C_FASTMODEPLUS_SCL);
	  HAL_FMPI2CEx_DisableFastModePlus(FMPI2C_FASTMODEPLUS_SDA);
}


// turn on/off I2C1 module
void control_I2C1_enable() {
	__HAL_RCC_I2C1_CLK_ENABLE();
}
void control_I2C1_disable() {
	__HAL_RCC_I2C1_CLK_DISABLE();
}
// turn on/off I2C2 module
void control_I2C2_enable() {
	__HAL_RCC_I2C2_CLK_ENABLE();
}
void control_I2C2_disable() {
	__HAL_RCC_I2C2_CLK_DISABLE();
}
// turn on/off I2C3 module
void control_I2C3_enable() {
	__HAL_RCC_I2C3_CLK_ENABLE();
}
void control_I2C3_disable() {
	__HAL_RCC_I2C3_CLK_DISABLE();
}


// turn on/off SPI1 module
void control_SPI1_enable() {
	__HAL_RCC_SPI1_CLK_ENABLE();
}
void control_SPI1_disable() {
	__HAL_RCC_SPI1_CLK_DISABLE();
}
// turn on/off SPI2 module
void control_SPI2_enable() {
	__HAL_RCC_SPI2_CLK_ENABLE();
}
void control_SPI2_disable() {
	__HAL_RCC_SPI2_CLK_DISABLE();
}
// turn on/off SPI3 module
void control_SPI3_enable() {
	__HAL_RCC_SPI3_CLK_ENABLE();
}
void control_SPI3_disable() {
	__HAL_RCC_SPI3_CLK_DISABLE();
}


// turn on/off TIM2 input capture interrupt
void control_TIM2_it_enable(void) {
    HAL_TIM_IC_Start_IT(&htim2, TIM_CHANNEL_1);
}
void control_TIM2_it_disable(void) {
    HAL_TIM_IC_Stop_IT(&htim2, TIM_CHANNEL_1);
}
// turn on/off TIM2 module
void control_TIM2_enable() {
	__HAL_RCC_TIM2_CLK_ENABLE();
}
void control_TIM2_disable() {
	__HAL_RCC_TIM2_CLK_DISABLE();
}

// ******************************************************************************************

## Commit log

2024-11-28 create bill of material file
    [BOM.xlsx]
2024-11-28 pcb folder has been created
2024-11-28 pcb files upload
    [PCB1.PcbDoc, PCrs_20.PrjPcb, Sheet1.SchDoc]
2024-12-28 PCB update
    [PCB1.PcbDoc, PCrs_20.PrjPcb, Sheet1.SchDoc]
2024-12-28 PCB update, KEYS
    [PCB1.PcbDoc, Sheet1.SchDoc]
2024-12-29 PCB update - keys & lights routing
    [Sheet1.SchDoc]
2024-12-30 PCB final update - review required
    [PCrs_20.PrjPcb, Sheet1.SchDoc]
2024-12-30 PCB final update 2 & gerber generation
    [PCB1_Bottom_3D_Body.gbr, PCB1_Bottom_Assembly.gbr, PCB1_Bottom_Component_Center.gbr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]
2024-12-31 PCB final update 3 & gerber generation
    [PCB1_Bottom_3D_Body.gbr, PCB1_Bottom_Assembly.gbr, PCB1_Bottom_Component_Center.gbr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]
2025-01-08 BOM update
    [BOM.xlsx]
2025-02-08 repositorium complex clean
    [BOM.xlsx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]
2025-02-08 PCrs ver 2.0 upload
    [PCB1_Bottom_3D_Body.gbr, PCB1_Bottom_Assembly.gbr, PCB1_Bottom_Component_Center.gbr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]
2025-03-15 PCrs ver 2.1 upload
    [PCB_Bottom_3D_Body.gbr, PCB_Bottom_Assembly.gbr, PCB_Bottom_Component_Center.gbr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]
2025-03-22 MPU & PSU pcb schematics created
    [MPU.SchDoc, PCrs_30.PrjPcb, PowerSupply.SchDoc]
2025-03-22 buck converter circuit were added, 3.3v out voltage
    [PCrs_30.PrjPcb, PowerSupply.SchDoc]
2025-03-29 board version designation update
2025-11-27 Altium Files upd, first ver of PCB complete
    [Buffers.SchDoc, Connectors.SchDoc, MPU.SchDoc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]
2025-11-27 clean up
    [Mainboard_Bottom_3D_Body.gbr, Mainboard_Bottom_Assembly.gbr, Mainboard_Bottom_Component_Center.gbr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]
2025-12-21 block diagram upd, power labels fix
2026-05-02 names of catalogs upd
    [Buffers.SchDoc, Connectors.SchDoc, MPU.SchDoc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]
2026-05-19 drivers added

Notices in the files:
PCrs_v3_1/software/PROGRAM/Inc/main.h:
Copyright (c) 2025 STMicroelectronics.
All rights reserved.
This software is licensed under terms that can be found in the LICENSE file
